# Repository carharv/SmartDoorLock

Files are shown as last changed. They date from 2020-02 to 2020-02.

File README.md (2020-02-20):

# Smart Door Lock by Carson Harvey
This project turns any deadbolt door lock, without permanent modification, into an electronic IOT lock with a NodeMCU ESP8266 and a servo. The lock is connected to the internet through Blynk and can be controlled through a phone app, NFC tag in combination with IOS shortcuts / Android Tasker, and a physical button.  

**Items needed:**
  - NodeMCU ESP8266: ~$5 each (http://bit.ly/AmazonNodeMCU)
  - TowerPro MG995R High Torque Servo: ~$20 each (http://bit.ly/adafuitservo)
  - Push Button: ~$0.30 each (http://bit.ly/AmazonPushButtons)
  - Jumper Wires: ~$6 for 120 (http://bit.ly/AmazonJumperWires)
  - NFC Tags: ~$6 for 10 (http://bit.ly/AmazonNFCTags)
  - Access to a 3D Printer to make the enclosure
  - 2 MicroUSB cables
  - Soldering iron and solder
  - Wire cutter
  - Wire stripper
  
  Total new materials cost: ~$40
  
  **Blynk Setup:**
   1. Download the blynk app on your mobile device.
   2. Create a new project and name it whatver you would like. Choose ESP8266 as the device and WiFi for the connection type. 
   3. Once you make the project you should receive an Auth Token in your email. You will need this later when setting up the ESP8266.
   4. Click anywhere in the project area and add a button. Name it whatever you'd like. Set the output to be V0 with 0 and 1 being the          options. Change the mode to switch, and label the on and off to be whatever you'd like.
   5. Select the project area again and add the notification widget. 
   6. If you have multiple people that you would like to grant access to the lock you can go into the project settings and generate a            link to share with others. 
    
   **ESP8266 Setup:**
   1. Plug it into your computer with a micro usb cable. Make sure that the cable is not just power only! 
   2. Download Arduino IDE here: https://www.arduino.cc/en/main/software
   3. Make sure that you have installed the proper drivers for the ESP8266 as well. Those can be found here:                                  https://github.com/nodemcu/nodemcu-devkit/tree/master/Drivers
   4. In the Arduino IDE go to File -> Preferences and make sure that this URL is in the Additional Boards Manager URLs section:              http://arduino.esp8266.com/stable/package_esp8266com_index.json
   5. Under the Tools tab, go to manage libraries and search for and install Blynk, and also make sure that the Servo library is              updated and installed as well.
   6. Under the Tools tab, select Board -> Boards Manager and then search for ESP8266. Install the latest version. 
   7. Back under the Tools tab select Board and then choose the NodeMCU 1.0 (ESP-12 Module) from the list. 
   8. Still under the Tools tab change CPU frequency to 80 Mhz, the upload speed to 921600, and the flash size to 4MB (FS:3MB...)
   9. Copy and paste the code from SmartLock.ino in this repository, or download and open the file in the Arduino IDE. 
   10. Enter in your Blynk Auth Token and WiFi details in their respective fields.
   11. You may need to adjust the lockedState and unlockedState variables depending on your lock. 
   12. Once you are ready to upload the code go to the Sketch tab and click the upload button.
   
   **3D Printed Enclosure:**
   
   You can download the STL files in the repository. If you don't personally have a 3D printer, most public libraries and universities      have one. Additionally, you can use a service like ShapeWays to have the parts printed and mailed to you. Feel free to design and        print your own enclosure, or make it out of wood or something.
   
   **Connecting everything together:**
   
   Circuit Diagram
   
   1. Start by modifying one of the USB cables to supply power to the servo. Cut MicroUSB connector off of the end of the cable. Strip         back the sheathing on the positive (usually red) wire and the negative (usually black) wire. The other wires are not necessary for       powering the servo and can be cut away or folded back. Take three of the male to female jumper wires and cut the female ends off         of them. Strip back some of the sheathing and solder one jumper wire to the positive USB wire and the other two jumper wires to         the negative USB wire. Use electrical tape or heatshrink to strengthen and protect the solder joints. What you should be left with       is a male USB plug on one end and three male jumper wires on the other end (one connected to positive, two connected to ground). 
   2. Connect the positive USB jumper wire to the positve wire and one of the negative USB jumper wires to the negative wire on the           servo. Connect the other negative jumper wire to a GND pin on the ESP8266. 
   3. Take another male to female jumper wire and connect the male end to the signal (usually yellow) wire on the servo. Connect the           female end to pin D4 (GPIO 2) on the ESP8266.
   4. Take two male to female jumper wires and cut the male ends off. Strip back some of the sheathing and solder one wire to the             positive terminal on the button and the other jumper wire to the negative terminal on the button. 
   5. Connect one of the jumper wires that is connected to the button to a GND pin on the ESP8266 and the other jumper wire to the TX         (GPIO 0) pin.
   6. Once everything is connected, power the ESP8266 with a MicroUSB cable and plug the servo power USB cable in as well. 
   7. At this point, everything should be working. Test it out by pushing the physical button or the button in the Blynk app. 
   8. If all is working as it should, attach everything to the 3D printed housing and stick it on the door. I used velcro command strips       to make the entire thing easily removable. 
   
   **Setting up the NFC tags:**

   I have an iPhone so these steps will be specific to the Shortcuts app, but it should be very similar on the Android Tasker app. 
   
   1. Download the Shortcuts app if you haven't already and open it.
   2. Go to the Automation tab and click the blue + in the upper right. 
   3. Select Personal Automation.
   4. Scroll down and select the NFC option.
   5. Click the scan button and tap your phone on one of the NFC stickers. The NFC reader on the iPhone 11 is in the upper middle             section on the back of the phone.
   6. Once you have the NFC tag scanned, set the action to Get Contents of URL.
   7. The URL will be the IP address of Blynk's server in combination with your Blynk Auth Token. To find the Blynk IP address, open a         command or terminal window and ping Blynk-Cloud.com. At the time of writing it is 45.55.96.146. This is how the URL should look:
      **http://45.55.96.146/YOURAUTHTOKEN/update/V0?value=0**
      This shortcut will unlock the door whenever your phone scans the NFC tag. Repeat the above steps to make a shortcut that locks the       door, but change the *value=0* at the end of the URL to *value=1*. Once you have the shortcuts made, you can click on them and           toggle the Ask Before Running setting to off so that the door will unlock/lock as long as your screen is awake. I have also foound       that shortcuts do not run while on a FaceTime call. 

      Thats it! Enjoy the convenience of your new smart lock. If you have any questions I will try to answer them as best as I can.

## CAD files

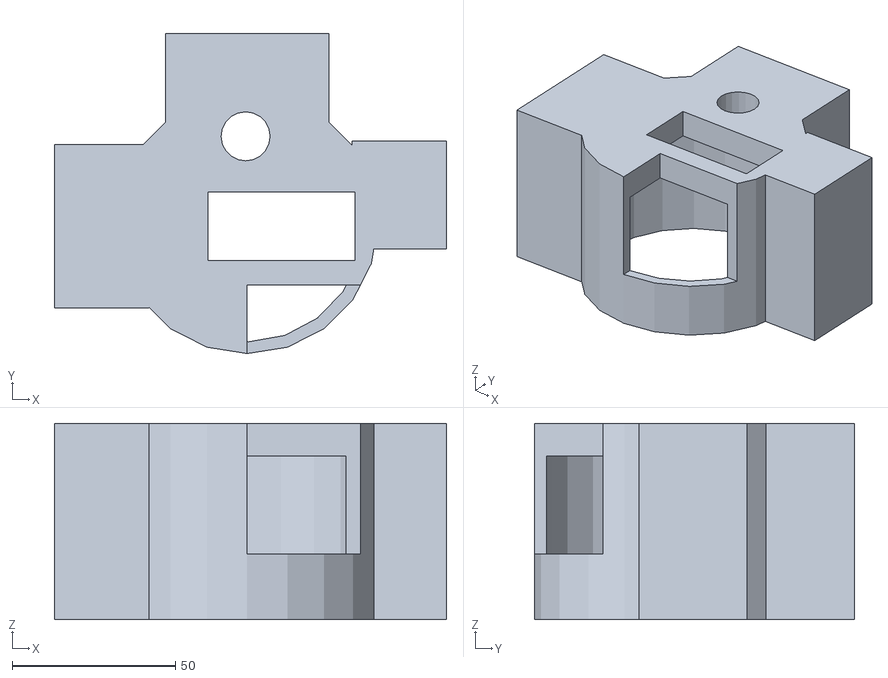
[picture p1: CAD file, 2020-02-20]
SmartDoorLockHousingV2.stl
120.0 x 98.0 x 60.0

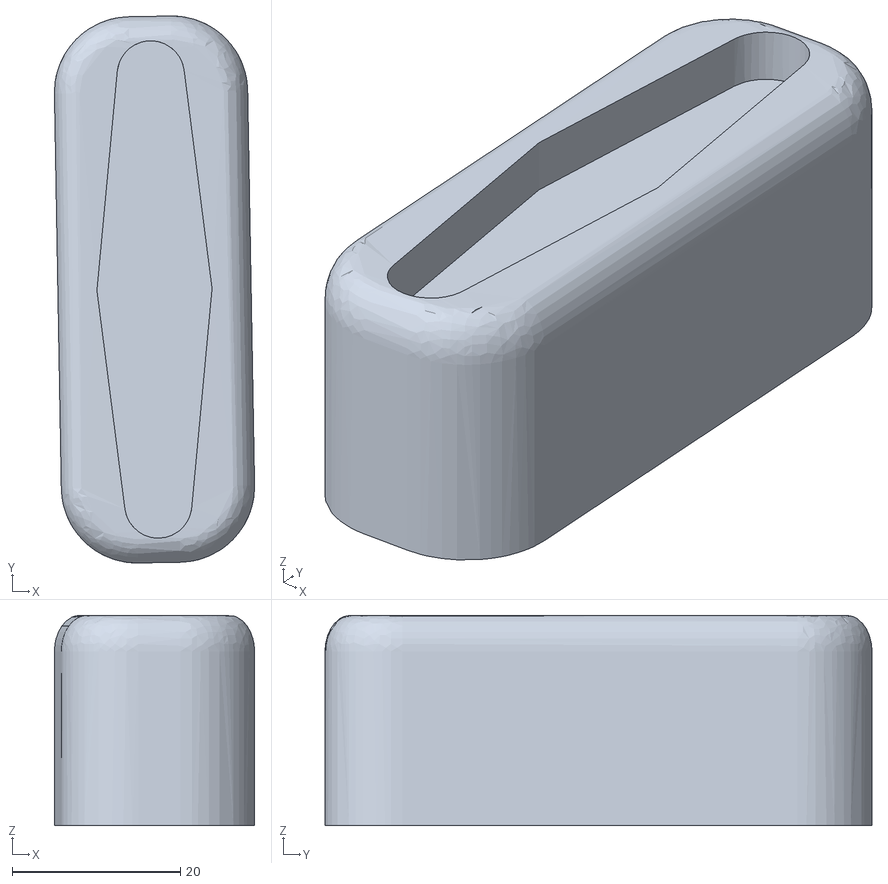
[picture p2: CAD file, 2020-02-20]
ServoToLockAdapter.stl
23.8 x 65.1 x 25.0

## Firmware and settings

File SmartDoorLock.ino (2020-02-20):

/* Copyright (c) 2020 Carson Harvey
   This code is licensed under GNU General Public License v3.0 */

#include <ESP8266WiFi.h>
#include <BlynkSimpleEsp8266.h>
#include <Servo.h>

char auth[] = "PASTE HERE"; /* Blynk Auth Token */
char ssid[] = "ENTER HERE"; /* WiFi name */
char pass[] = "ENTER HERE"; /* WiFi Password */
const int lockedState = 115; /* Degree the servo rotates to when locked. You may need to tweak this depending on your door. */
const int unlockedState = 20; /* Degree the servo rotates to when unlocked. You may need to tweak this depending on your door. */
const int buttonPin = 1; /* pin that physical button is conncected to */
int buttonState = 0; 
boolean toggle = true; 

Servo servo; 

BLYNK_WRITE(V0)
  {
  int lockState = param.asInt();
  if (lockState == 1) { /* If the button in blynk app is clicked */
    servo.attach(2); /* Attach servo on GPIO 2 (physical pin D4) */
    servo.write(lockedState); /* lock door */
    Blynk.notify("The door has been locked!");
    delay(750); /* Wait 750 ms */
    servo.detach(); /* Detach the servo to prevent stripping the gears if the door is manually unlocked */
    }
  else {
    servo.attach(2); /* Attach servo on GPIO 2 (physical pin D4) */
    servo.write(unlockedState); /* otherwise if lock state is 0, unlock door */
    Blynk.notify("The door has been unlocked!");
    delay(750); /* Wait 750 ms */
    servo.detach(); /* Detach the servo to prevent stripping the gears if the door is manually unlocked */
    }
  }

void setup()
{
  Blynk.begin(auth, ssid, pass); /* Connects to Blynk */
  pinMode(buttonPin, INPUT); /*Sets the button pin as an input */
  digitalWrite(1, HIGH); /* Sets the button pin to the high (unpressed) state as default */
}

void loop()
{
  buttonState = digitalRead(buttonPin); /* reads the current state of the button */
  if (buttonState == LOW) /* if the button is pressed */
  {
    if(toggle)
    {
      servo.attach(2); /* Attach servo on GPIO 2 (physical pin D4) */
      servo.write(lockedState); /* lock the door */
      toggle = !toggle;
      delay(750); /* Wait 750 ms */
      servo.detach(); /* Detach the servo to prevent stripping the gears if the door is manually unlocked */
    }
    else
    {
      servo.attach(2); /* Attach servo on GPIO 2 (physical pin D4) */
      servo.write(unlockedState);
      toggle = !toggle;
      delay(750); /* Wait 750 ms */
      servo.detach(); /* Detach the servo to prevent stripping the gears if the door is manually unlocked */
    }
    delay(500);
  }
  
  Blynk.run(); /* Communication with Blynk */
 
}
